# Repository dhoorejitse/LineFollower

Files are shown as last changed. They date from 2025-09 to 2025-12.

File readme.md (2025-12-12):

# LineFollower

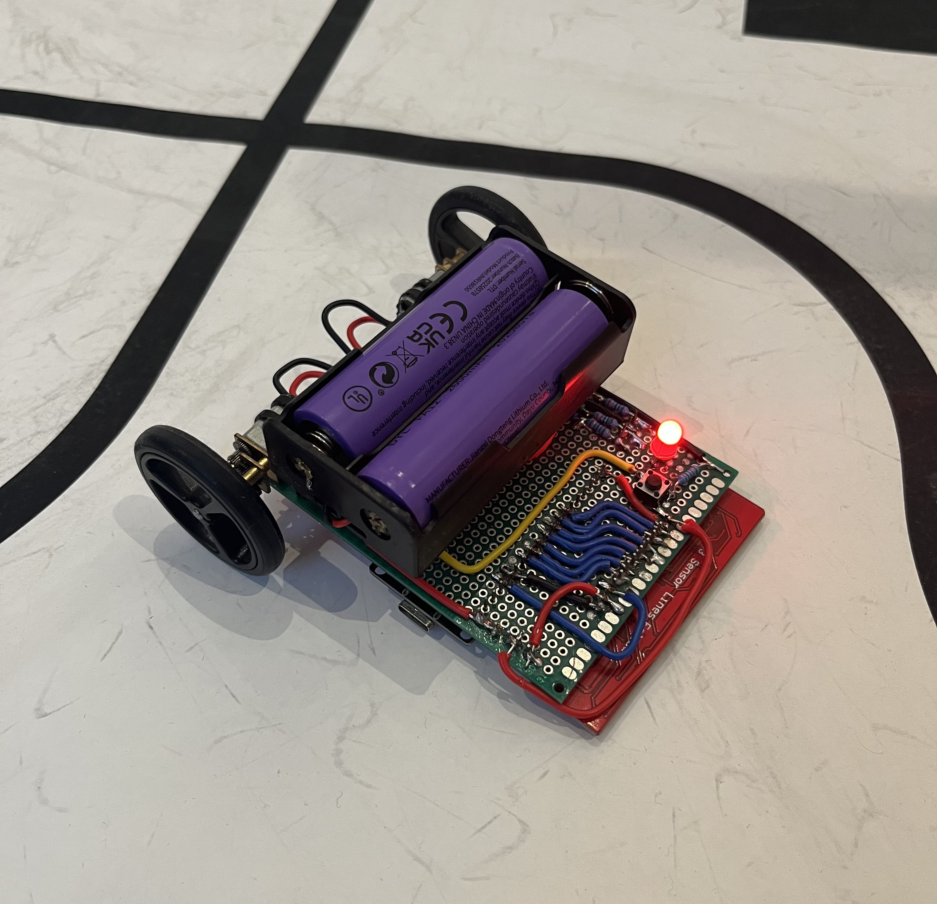
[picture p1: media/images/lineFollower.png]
lineFollower


## specifications

microcontroller: ESP32 NodeMCU Dev Board

motors: Aslong JGA12-N20-30 6V

h-bridge: DRV8833 H-Bridge Module

sensors: HY-S301

batteries: 2x18650

wireless communication: CP2102 (μC)

distance sensor - motors: 9cm

weight: 185g

speed: 0.6m/s

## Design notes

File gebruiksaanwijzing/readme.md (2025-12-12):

# Gebruiksaanwijzing

### gebruiken van esp32 in arduino IDE
* esp library intalleren
* boards toevoegen in preferences
* CP2102 drivers installeren

### opladen / vervangen batterijen
Het opladen van de batterijen gebreurd met een speciale batterijoplader die gemaakt is op de 18650 batterijen veillig en correct op te laden. Vervang de batterijen door de lege batterijen uit de houder te halen en vervang deze met opgeladen batterijen

### draadloze communicatie
#### verbinding maken
zorg dat de robot aanstaat (rgb led is rood/groen). Verbind vervolgens uw pc met bluetooth device "ESP32_BT_DJ". Maak vervolgens een seriele verbinding in PuTTy:
* Serial line: Gebruik de 2de bluetooth COM poort in de device manager
* Speed: 115200
* Connection type: Serial

#### commando's
help
debug  
run true
run false
set cycle [µs]  
set power [0..255]  
set diff [0..1]  
set kp [0..]  
set ki [0..]  
set kd [0..]  
calibrate black  
calibrate white  

### kalibratie
plaats de robot op een volledig zwarte ondergrond
* commando: calibrate black

plaats de robot op een volledig witte ondergrond
* commando: calibrate white

controlleer of de waarden binnen het gewenste waarden geven
* commando: debug

### settings
De robot rijdt stabiel met volgende parameters:  
* cycle: 1000
* power: 200
* diff: 0.4
* kp: 18
* ki: 0
* kd: 0.2

### start/stop button
de robot kan gestart worden op twee manieren:
* fysieke button vooraan de robot gelegen
* commando: run true/false

de status van de robot wordt aangeduid met behulp van een rgb led
* rode led: run false
* groene led: run true

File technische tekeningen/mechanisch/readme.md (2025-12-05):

# Technische tekeningen mechanisch

volgende zaken zitten in de mechanische technische tekeningen

* onderdelen
* samenstellingen

Deze werden vooral gebruikt in eerste instantie om na te gaan wat de beste positie was voor elk component + uitlijnen van wielen en sensor, etc.

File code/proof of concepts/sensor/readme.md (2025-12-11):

# Sensor - PoC
Deze PoC vererifieert de werking van volgende zaken:
- minimaal 6 sensoren kunnen onafhankelijk van elkaar worden uitgelezen (geen calibratie, normalisatie of interpolatie)
- Hierbij moet een zo groot mogelijk bereik van de AD converter benut worden (indien van toepassing)

Bij een correcte werking zal de sensor een hoge waarde geven bij lichte kleuren (max 4095) en een lage waarde bij donkere kleuren

https://github.com/user-attachments/assets/09217cbb-010d-4b2e-adb0-6ba14c347263

## Schema
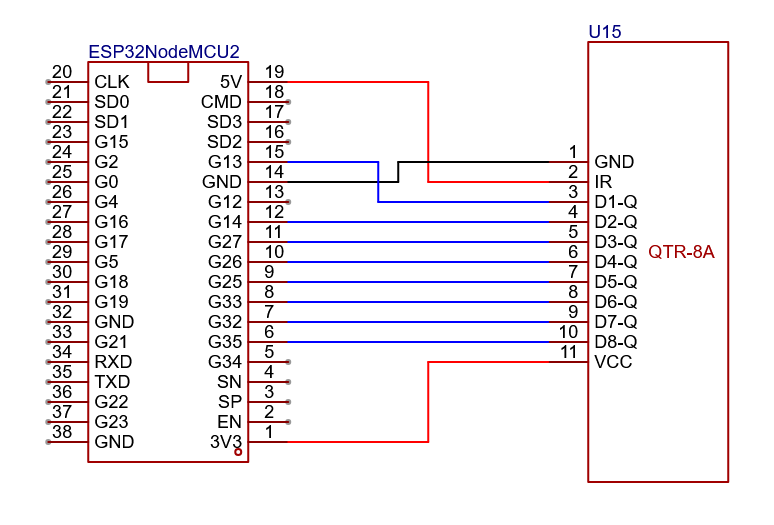
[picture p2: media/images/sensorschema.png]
Schema


## Stappenplan
- Sluit de componenten correct aan volgens bovenstaande schema
- Verbind de microcontroller met de pc
- Verify/Upload de code naar de mictrocontroller
- Verifieer de werking door te vergelijken met bovenstaande video

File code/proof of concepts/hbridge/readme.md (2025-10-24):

# H-Bridge - PoC
Deze PoC vererifieert de werking van volgende zaken:
- 2 motoren kunnen onafhankelijk van elkaar kunnen draaien
- motoren zijn (traploos) regelbaar in snelheid en draairichting

Bij een correcte werking zal eerst motor 1 traploos versnellen van stilstand tot zijn maximum snelheid, en vervolgens terug vertragen in de andere richting tot stilstand. Motor 2 herhaald deze werking.

https://github.com/user-attachments/assets/9430dffd-f219-440d-9be8-ca7bf7144678

## Schema
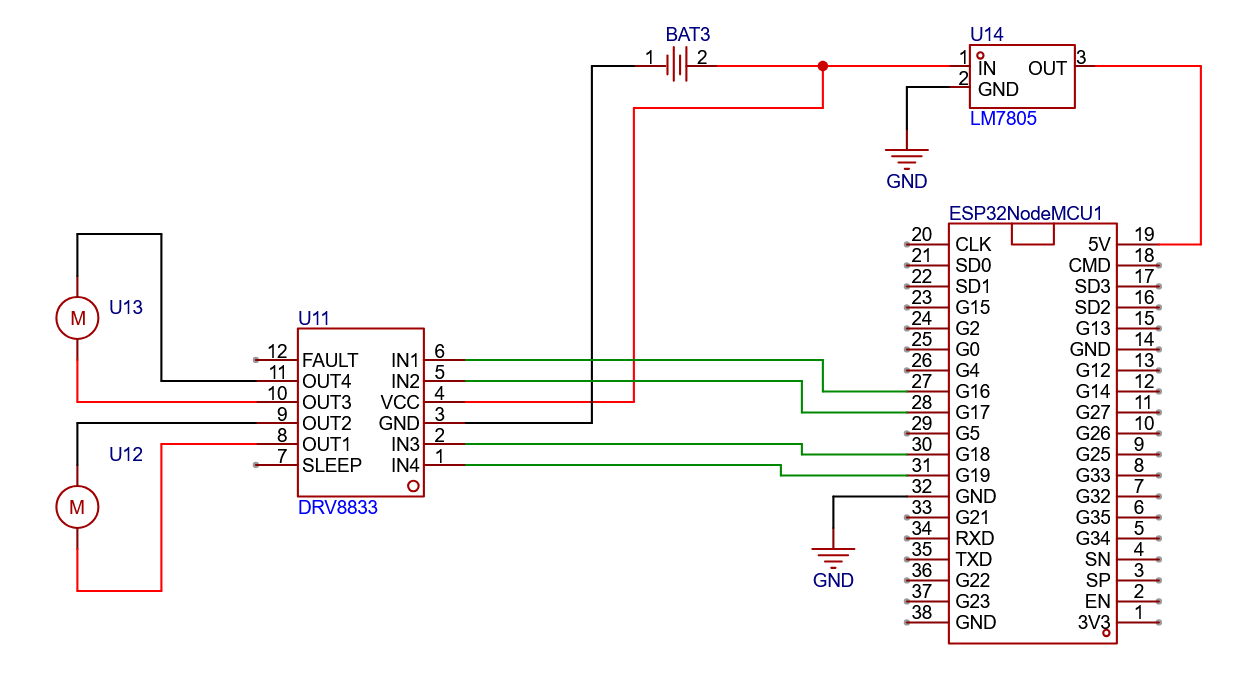
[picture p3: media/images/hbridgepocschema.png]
Schema


## Stappenplan
- Sluit de componenten correct aan volgens bovenstaande schema
- Verbind de microcontroller met de pc
- Verify/Upload de code naar de mictrocontroller
- Verifieer de werking door te vergelijken met bovenstaande video

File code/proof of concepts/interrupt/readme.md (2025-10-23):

# Interrupt - PoC
Deze PoC vererifieert de werking van volgende zaken:
- start/stop met drukknop
- gebruikmakend van een hardware interrupt

Bij een correcte werking zal de blink cyclus blijven doorlopen, wanneer de drukknop kortstondig word ingedrukt word de cyclus onderbroken en blijft de RGB led op wit. Bij een 2de keer drukken op de drukknop zal de cyclus hervatten

https://github.com/user-attachments/assets/07a7d600-da04-43f0-961d-6ccd3eb3b6cc

## Schema
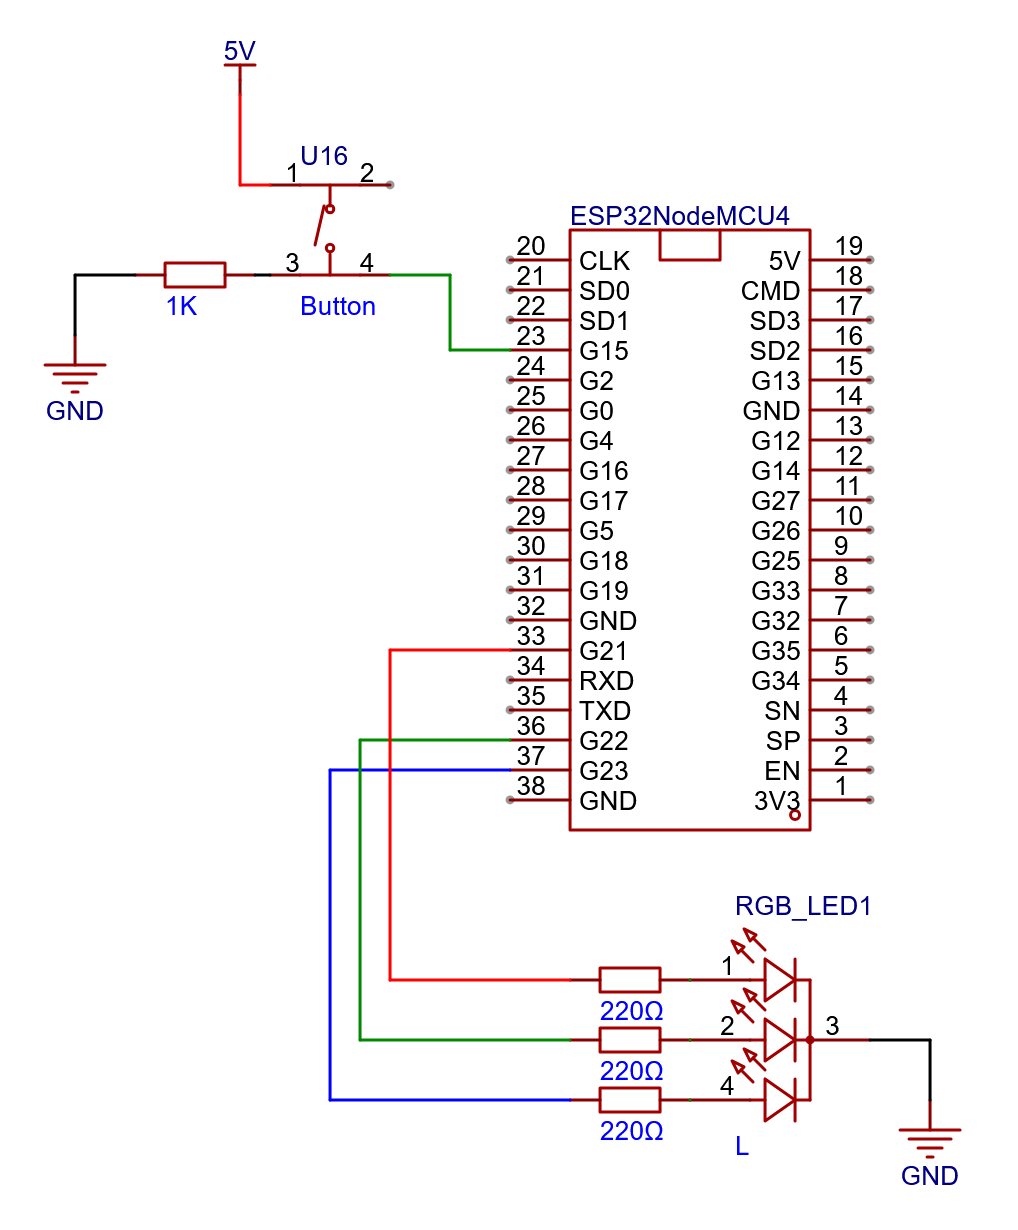
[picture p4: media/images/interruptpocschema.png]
Schema


## Stappenplan
- Sluit de componenten correct aan volgens bovenstaande schema
- Verbind de microcontroller met de pc
- Verify/Upload de code naar de mictrocontroller
- Verifieer de werking door te vergelijken met bovenstaande video

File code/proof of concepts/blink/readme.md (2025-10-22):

# Blink - PoC
Deze PoC vererifieert de werking van volgende zaken:
- compilen en uploaden van een programma naar de microcontroller lukt
- de klok frequentie van de microcontroller klopt

Bij een correcte werking knippert de RGB-led achtereenvolgens rood, groen en blauw, telkens 1 seconde aan en 1 seconde uit, waarna de cyclus zich herhaalt. Bij een opstart of reset van de microcontroller knippert de led 3 keer kortstondig wit.

https://github.com/user-attachments/assets/0f00047d-495a-4bb4-b6ac-76eb2669470c

## Schema
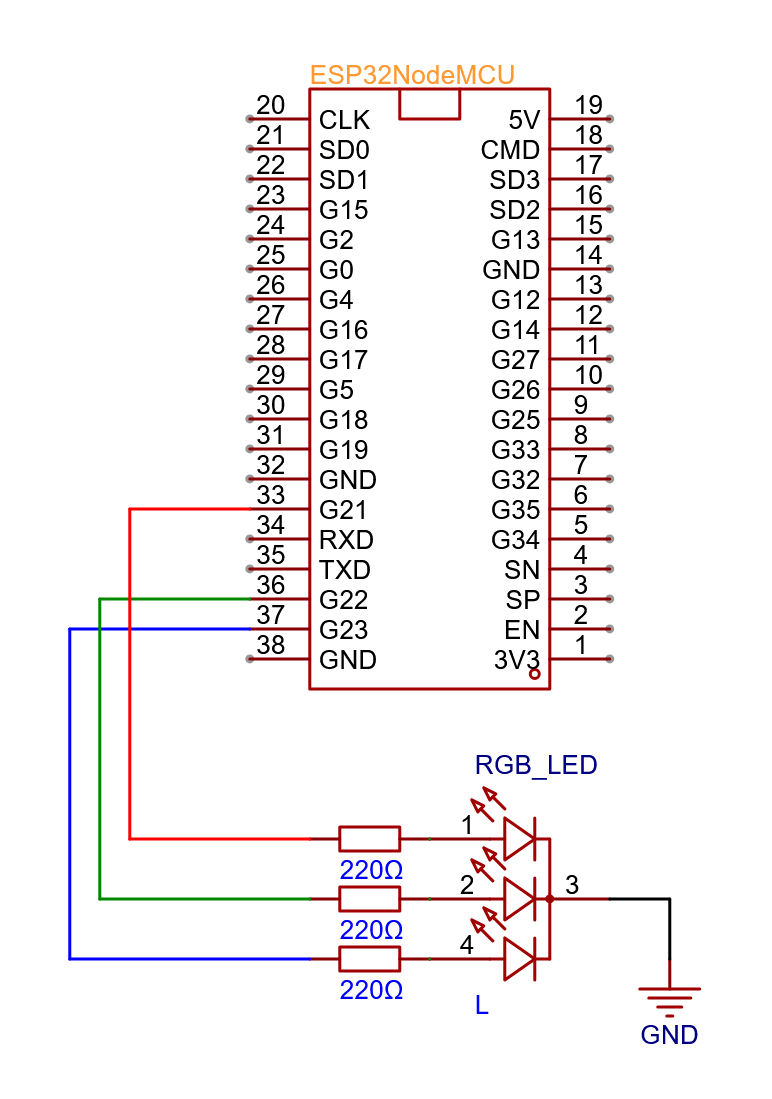
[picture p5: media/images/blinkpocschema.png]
Schema


## Stappenplan
- Sluit RGB led samen met weerstanden correct aan op de microcontroller volgens bovenstaande schema
- Verbind de microcontroller met de pc
- Verify/Upload de code naar de mictrocontroller
- Verifieer de werking door te vergelijken met bovenstaande video

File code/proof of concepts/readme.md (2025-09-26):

# Proof of Concepts

Een proof of concept is een combinatie van minimale hard- en software om eenvoudig aan te tonen dat iets werkt.  
Proof of concepts kunnen enerzijds als eerste poging dienen om een bepaald onderdeel van het project werkend te krijgen. Anderzijds kunnen ze tijdens het debuggen van het finale project dienen als test om eventuele hardware problemen te elimineren bij onduidelijke problemen.
<br />  
<br />
Een proof of concept bestaat uit
* een elektronisch schema (indien van toepassing)
* minimale code om de voorop gestelde zaken te demonstreren
* minimale uitleg / aandachtspunten
<br />
De elektronische schakelingen van de proof of concepts komen bij voorkeur overeen met deze van de uiteindelijke linefollower, zodat de code zonder aanpassingen op het finale project kan draaien.

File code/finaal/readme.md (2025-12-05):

# finaal programma

Dit is de volledige werkende code.

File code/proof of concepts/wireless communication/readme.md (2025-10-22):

# communicatie - PoC
Deze PoC vererifieert de werking van volgende zaken:
- er kan duplex gecommuniceerd worden tussen de microcontroller en een laptop
- gebruikmaken van PuTTy

Bij een correcte werking zal de seriële monitor berichten ontvangen van PuTTY, en zal PuTTy berichten ontvangen van de seriële monitor.

https://github.com/user-attachments/assets/d7bfd74a-13d0-45ac-b519-173b7eff39de

## Schema
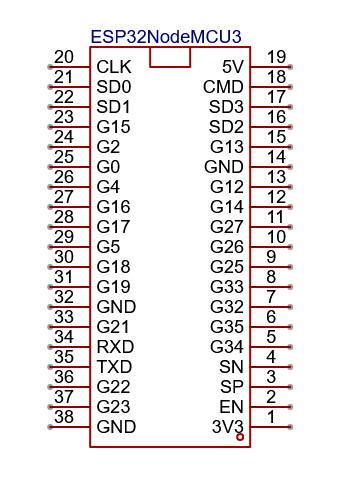
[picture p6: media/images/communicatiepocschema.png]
Schema


## Stappenplan
- Verbind de microcontroller met de pc
- Verify/Upload de code naar de mictrocontroller
- Controleer of de bibliotheek BluetoothSerial.h is geïnstalleerd
- Verbind met "ESP_BT_DJ" via bluetooth op laptop
- kijk in device manager welke COM word gebruikt door de bluetooth verbinding
- Connecteer via PuTTY met deze seriële COM en stel de correcte baudrate in
- Verifieer de werking door te vergelijken met bovenstaande video

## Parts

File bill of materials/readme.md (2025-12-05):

## bill of materials
<br />

|volgnummer|naam|omschrijving|nieuw/recup|kostprijs/stuk|aantal|subtotaal|
|----|---|---|---|---|---|---|
| 01 | ESP32 NodeMCU Dev Board | Development Board WiFi + Wireless CP2102 Dual Core 2.4GHz Microcontroller | Nieuw | € 8.50 | 1 | € 8.50 |
| 02 | Aslong JGA12-N20-30 | DC-Transmissiemotor 6V - 30:1 - 500RPM | Nieuw | € 4.50 | 2 | € 9.00 |
| 03 | DRV8833 H-Bridge Module | Motor Driver Module 1.5A Dual H-Bridge | Nieuw | € 1.50 | 1 | € 1.50 |
| 04 | HY-S301 | 8x IR Sensor (QTR-8A) | Nieuw | € 3.50 | 1 | € 3.50 |
| 05 | 18650 | Li-on Batterij - 2600mAh | Nieuw | € 2.50 | 2 | € 5.00 |
| 06 | Batterij Houder | 2 Slot 18650 Houder | Nieuw | € 1.50 | 1 | € 1.50 |
| 07 | Prototype Board | Dual Sided 90x70mm Board | Nieuw | € 0.50 | 1 | € 0.50 |
| 08 | Pololu Wiel 40x7mm | Siliconen Wielen - 3mm D-uitgaande as | Nieuw | € 2.50 | 2 | € 5.00 |
| 10 | LEGO blokje | Kleine lego blokjes gebruikt als steun vooraan | Recup | | 2 | |
| 11 | LED | | Recup | | 1 | |
| 12 | Knop | | Recup | | 1 | |
| 13 | Draad | 22AWG | Recup | | x | |
| 14 | Krimpkousen | | Recup | | x | |
| 15 | Soldeerdraad | | Recup | | x | |
| 16 | Pin Headers | Male + Female | Recup | | x | |
| 17 | Soldeerpasta | | Recup | | x | |
| | | | | | | € 34.5 |

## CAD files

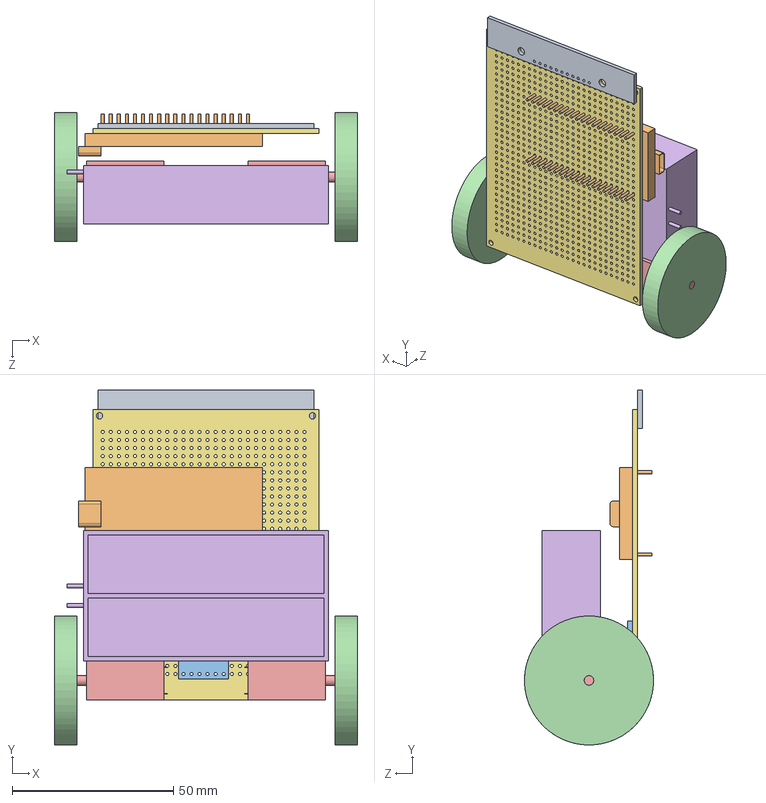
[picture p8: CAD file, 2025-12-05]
technische tekeningen/mechanisch/samenstellingen/LineFollower.SLDASM
94.0 x 110.0 x 40.0 mm
PrototypeBoard
BatteryHolder
Motor x 2
Wheel x 2
MotorDriver
Microcontroller
Sensor

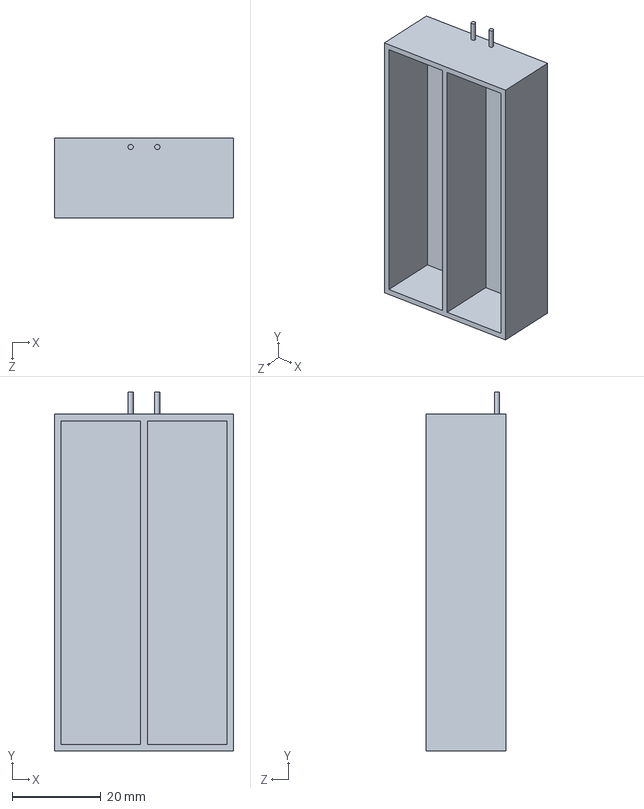
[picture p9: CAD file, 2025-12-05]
technische tekeningen/mechanisch/onderdelen/BatteryHolder.SLDPRT
40.5 x 81.0 x 18.0 mm

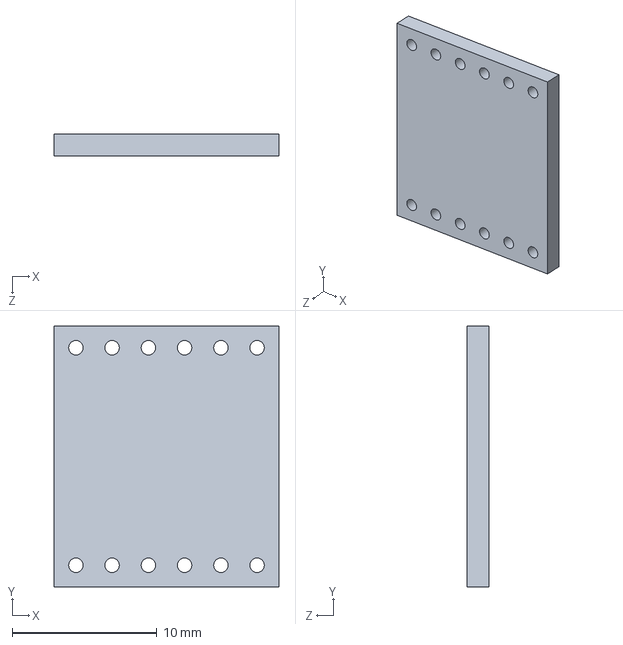
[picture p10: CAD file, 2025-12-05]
technische tekeningen/mechanisch/onderdelen/MotorDriver.SLDPRT
15.5 x 18.0 x 1.50 mm

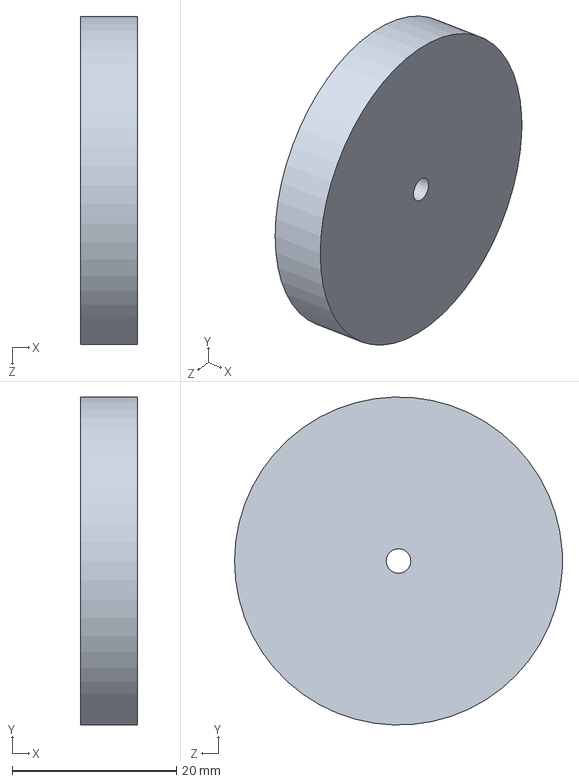
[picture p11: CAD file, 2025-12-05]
technische tekeningen/mechanisch/onderdelen/Wheel.SLDPRT
7.00 x 40.0 x 40.0 mm

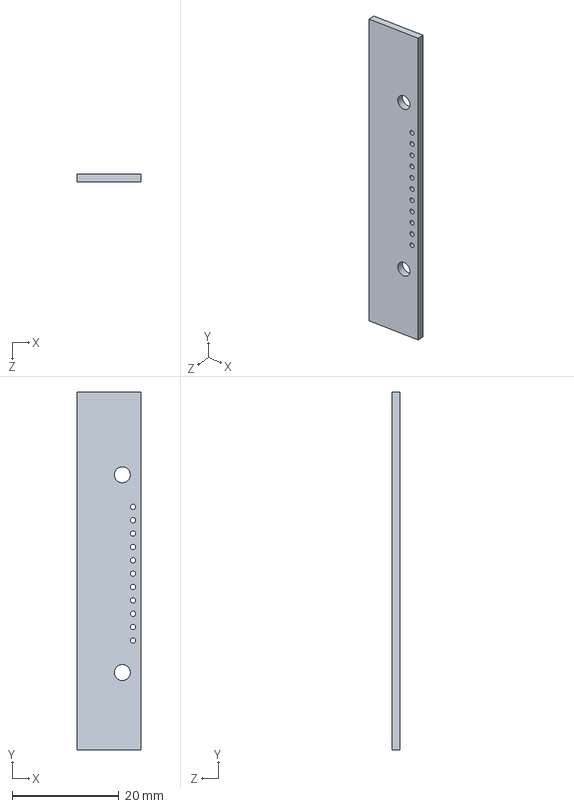
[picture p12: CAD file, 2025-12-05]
technische tekeningen/mechanisch/onderdelen/Sensor.SLDPRT
12.0 x 67.0 x 1.50 mm

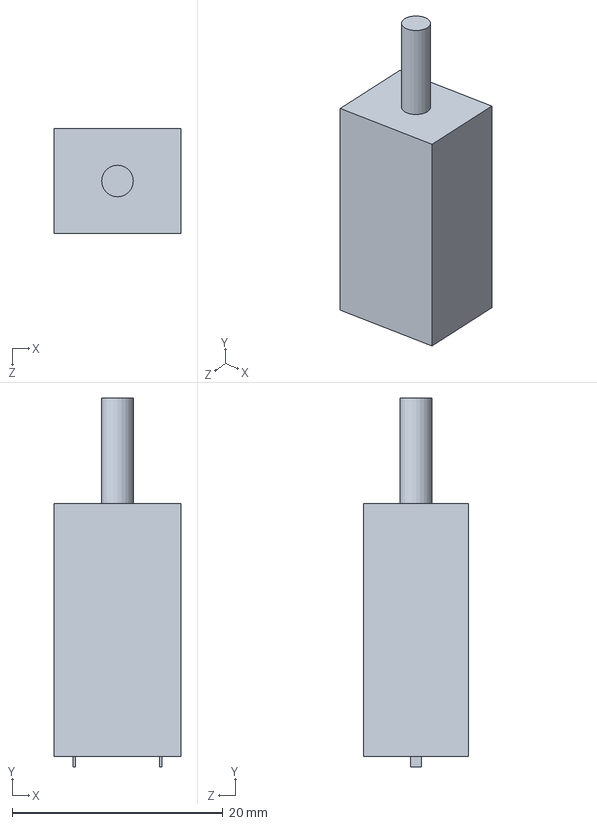
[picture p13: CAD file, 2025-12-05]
technische tekeningen/mechanisch/onderdelen/Motor.SLDPRT
12.0 x 35.0 x 10.0 mm

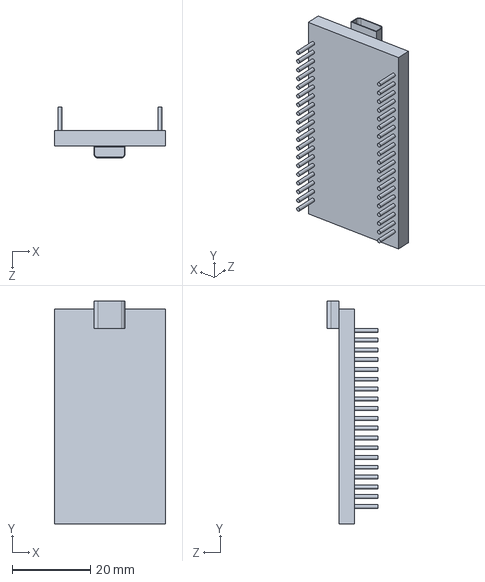
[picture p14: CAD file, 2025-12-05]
technische tekeningen/mechanisch/onderdelen/Microcontroller.SLDPRT
28.5 x 57.0 x 13.0 mm

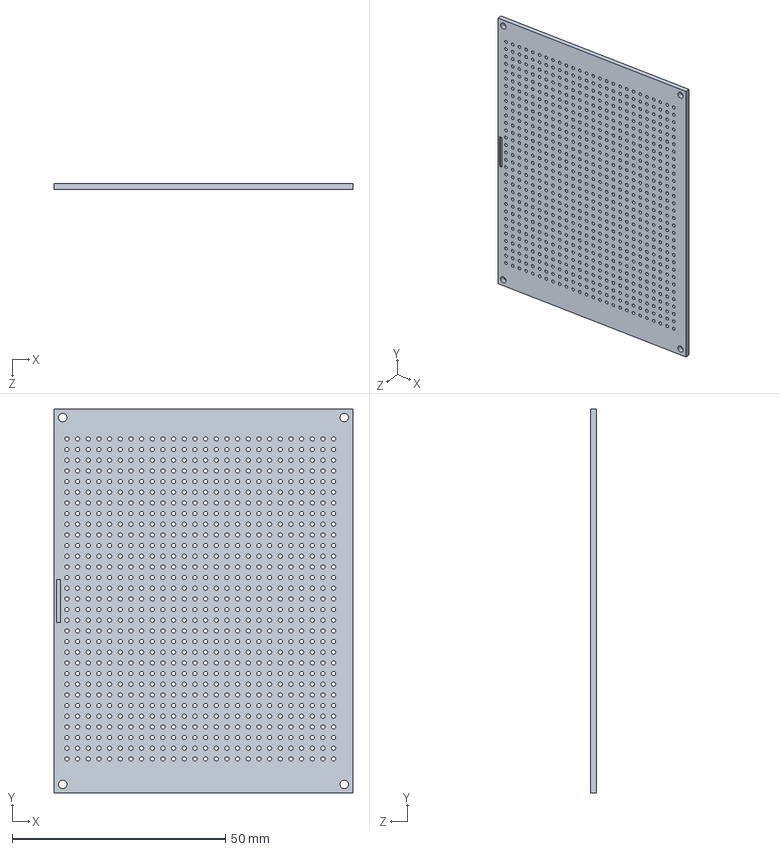
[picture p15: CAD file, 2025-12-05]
technische tekeningen/mechanisch/onderdelen/PrototypeBoard.SLDPRT
70.0 x 90.0 x 1.50 mm

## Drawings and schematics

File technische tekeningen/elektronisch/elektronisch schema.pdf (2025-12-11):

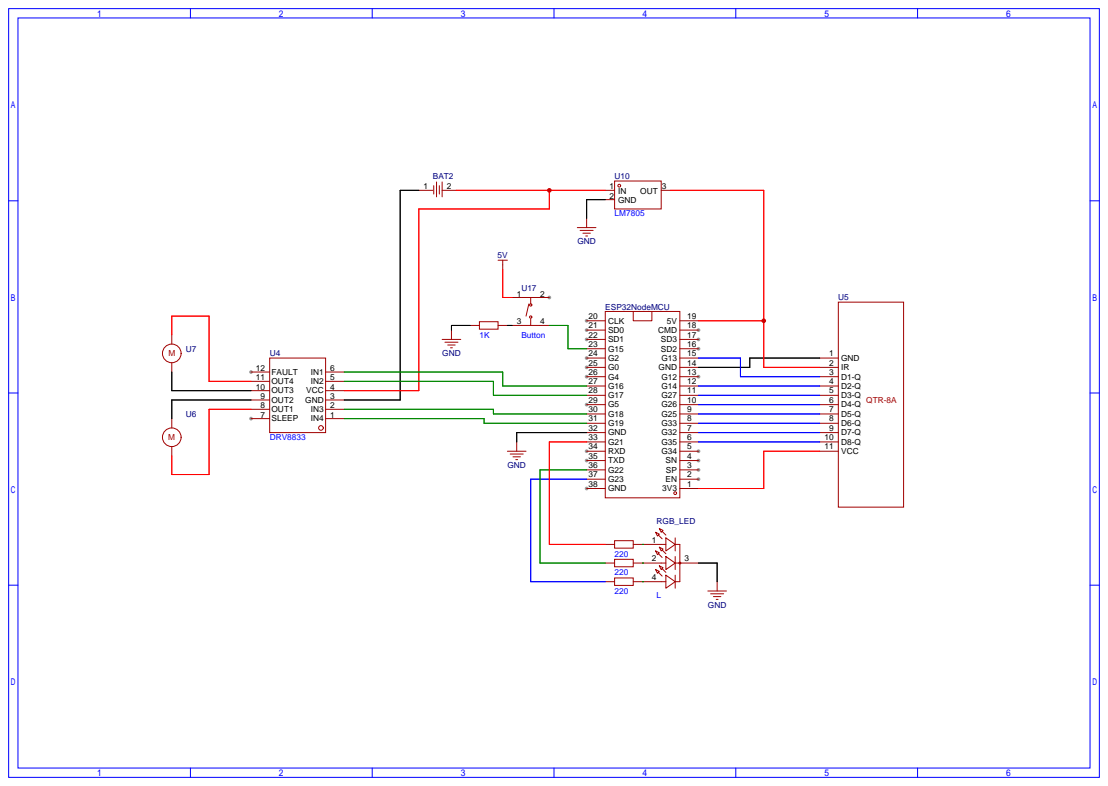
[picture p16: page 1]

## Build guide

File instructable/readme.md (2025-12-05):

# Instructable

### stap 1
bestel alle componenten uit de bill of materials  

### stap 2
soldeer de microcontroller, hbrug, sensor, en andere componenten op het prototype bord

### stap 3
soldeer de verbindingen tussen de componenten volgens de technische tekeningen

### stap 4 
maak boor 2 gaten op het einde van het prototype bord, bevesting met behulp van deze boringen de motoren aan het bord. (voeg secondelijm toe voor een sterkere verbinging)

### stap 5
schuur een blokje lego naar de juiste afmetingen en bevestig dit met secondelijm aan de sensor

### stap 6
soldeer pin headers op het bord en kleef pin headers vast aan de batterijhouder. Zo kan deze bevestigd worden aan het bord en snel los en vast gemaakt worden. Soldeer de verbindingen van de batterijhouder. (voeg krimpkousen toe om kortsluiting te voorkomen)

### stap 7
verbind de microcontroller met de pc gebruik maken van een USB-C kabel. Upload en compileer nu de finaal code naar de microcontroller, wacht tot deze volledig klaar is

### stap 8
de kabel mag nu uit de microcontroller worden getrokken

### stap 9
plaats de batterijen in de batterijhouder, de rgb led zou nu bij een correcte werking rood moeten branden

### stap 10
volg nu de stappen bij de gebruiksaanwijzing

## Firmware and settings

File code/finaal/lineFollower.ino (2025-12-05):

#include <Arduino.h>
#include "SerialCommand.h"
#include "EEPROMAnything.h"
#include <BluetoothSerial.h>

BluetoothSerial SerialPort;

void IRAM_ATTR handleButtonPress();
void updateRunLED();                  
void setColor(int r, int g, int b);

#define Baudrate 115200

#define MotorLeftForward 16
#define MotorLeftBackward 17
#define MotorRightForward 18
#define MotorRightBackward 19

const int pinR = 21;
const int pinG = 22;
const int pinB = 23;
const int buttonPin = 15;

volatile bool buttonPressed = false;
volatile unsigned long lastInterruptTime = 0;
const unsigned long debounceDelay = 200;

SerialCommand sCmd(SerialPort); // SerialPort for wired
bool debug = false;
bool run = false;
unsigned long previous, calculationTime; //set cycle time 2x calculationTime

const int sensor[] = {35,32,33,25,26,27,14,13};

struct param_t
{
  unsigned long cycleTime;
  int black[8]; //sensor
  int white[8]; //sensor
  int power;
  float diff;
  float kp;
  float ki;
  float kd;
  // add other paramaters here that need to be saved in memory 
} params;

int normalised[8];
float debugPosition;
float output;
float iTerm = 0;
float lastErr;

//*******************************************************************************// SETUP

void setup()
{
  Serial.begin(115200);
  SerialPort.begin("ESP32_BT_DJ");
  SerialPort.println("Verbonden");

  sCmd.setDefaultHandler(onUnknownCommand);
  sCmd.addCommand("help", onHelp);
  sCmd.addCommand("set", onSet);
  sCmd.addCommand("debug", onDebug);
  sCmd.addCommand("calibrate", onCalibrate);
  sCmd.addCommand("run", onRun);

  EEPROM.begin(512);
  EEPROM_readAnything(0, params);

  pinMode(pinR, OUTPUT);
  pinMode(pinG, OUTPUT);
  pinMode(pinB, OUTPUT);
  pinMode(buttonPin, INPUT);

  attachInterrupt(digitalPinToInterrupt(buttonPin), handleButtonPress, RISING);
  updateRunLED();

  SerialPort.println("ready");

  iTerm = 0;
}

//*******************************************************************************// LOOP

void loop()
{
  if (buttonPressed) 
  {
    buttonPressed = false;
    run = !run;
    if (run == false)
    {
      iTerm = 0;
    }
    updateRunLED();
  }

  sCmd.readSerial(); // listen and process serial commands

  unsigned long current = micros();
  if (current - previous > params.cycleTime)
  {
    previous = current;
    
    //measure & normalize
    for (int i = 0; i < 8; i++) normalised[i] = map(analogRead(sensor[i]), params.black[i], params.white[i], 0, 4096);

    //interpolate
    float position = 0;
    int index = 0;
    for (int i = 1; i < 8; i++) if (normalised[i] < normalised[index]) index = i;

    if (normalised[index] > 3000)
    {
      run = false; //can see if the robot is on a line or not, if not it, it will stop
      iTerm = 0;
      updateRunLED();
    }

    if (index == 0) position = -25;
    else if (index == 7) position = 25;
    else 
    {
      int sZero = normalised[index];
      int sMinusOne = normalised[index-1];
      int sPlusOne = normalised[index+1];

      float b = sPlusOne - sMinusOne;
      b = b / 2;

      float a = sPlusOne - b - sZero;

      position = -b / (2 * a);
      position += index;
      position -= 3.5;

      position *= 10;
    }
    debugPosition = position;

    float error = -position;
    output = 0;

    if (run) 
    {
      //proportional
      output = error * params.kp;

      //integration
      iTerm += params.ki * error;
      iTerm = constrain(iTerm, -510, 510);
      output += iTerm;

      //differentiation
      output += params.kd * (error - lastErr);
      lastErr = error;
    }
    else
    {
      iTerm = 0;
      output = 0;
    }

    output = constrain(output, -510, 510); //max en min PWM waarde motoren

    int powerLeft = 0;
    int powerRight = 0;

    if (run) if (output >= 0)
    {
      powerLeft = constrain(params.power + params.diff * output, -255, 255); //PWM motoren
      powerRight = constrain(powerLeft - output, -255, 255); //PWM motoren
      powerLeft = powerRight + output;
    }
    else
    {
      powerRight = constrain(params.power - params.diff * output, -255, 255); //PWM motoren
      powerLeft = constrain(powerRight + output, -255, 255); //PWM motoren
      powerRight = powerLeft - output;
    }

    // control motors
    analogWrite(MotorLeftForward, powerLeft > 0 ? powerLeft : 0);
    analogWrite(MotorLeftBackward, powerLeft < 0 ? -powerLeft : 0);
    analogWrite(MotorRightForward, powerRight > 0 ? powerRight : 0);
    analogWrite(MotorRightBackward, powerRight < 0 ? -powerRight : 0);
  }
  unsigned long difference = micros() - current;
  if (difference > calculationTime) calculationTime = difference;
}

//*******************************************************************************// SET

void onSet() //set commands
{
  char* param = sCmd.next();
  char* value = sCmd.next();

  if (strcmp(param, "cycle") == 0)
  {
    long newCycleTime = atol(value);
    float ratio = ((float) newCycleTime) / ((float) params.cycleTime);
    params.ki *= ratio;
    params.kd /= ratio;
    params.cycleTime = newCycleTime;
  } 
  else if (strcmp(param, "power") == 0) params.power = atol(value);
  else if (strcmp(param, "diff") == 0) params.diff = atof(value);
  else if (strcmp(param, "kp") == 0) params.kp = atof(value);
  else if (strcmp(param, "ki") == 0)
  {
    float cycleTimeInSec = ((float) params.cycleTime) / 1000000;
    params.ki = atof(value) * cycleTimeInSec;
  }
  else if (strcmp(param, "kd") == 0)
  {
    float cycleTimeInSec = ((float) params.cycleTime) / 1000000;
    params.kd = atof(value) / cycleTimeInSec;
  }
  else onUnknownParam((char*) param);

  EEPROM_writeAnything(0, params);
  EEPROM.commit();
}

//*******************************************************************************// CALIBRATE

void onCalibrate() //sensor calibration
{
  char* param = sCmd.next();

  if (strcmp(param, "black") == 0)
  {
    SerialPort.print("start calibrating black... ");
    for (int i = 0; i < 8; i++) params.black[i]=analogRead(sensor[i]);
    SerialPort.println("done");
  }
  else if (strcmp(param, "white") == 0)
  {
    SerialPort.print("start calibrating white... ");    
    for (int i = 0; i < 8; i++) params.white[i]=analogRead(sensor[i]);  
    SerialPort.println("done");      
  }
  else onUnknownParam((char*) param);

  EEPROM_writeAnything(0, params);
  EEPROM.commit();
}

//*******************************************************************************// DEBUG

void onDebug()
{
  SerialPort.print("cycle time: ");
  SerialPort.println(params.cycleTime);

  SerialPort.print("calculation time: ");
  SerialPort.println(calculationTime);
  calculationTime = 0;

  SerialPort.print("black: ");
  for (int i = 0; i < 8; i++)
  {
    SerialPort.print(params.black[i]);
    SerialPort.print(" ");
  }
  SerialPort.println(" ");

  SerialPort.print("white: ");
  for (int i = 0; i < 8; i++)
  {
    SerialPort.print(params.white[i]);
    SerialPort.print(" ");
  }
  SerialPort.println(" ");

  SerialPort.print("normalised: ");
  for (int i = 0; i < 8; i++)
  {
    SerialPort.print(normalised[i]);
    SerialPort.print(" ");
  }
  SerialPort.println(" ");

  SerialPort.print("position: ");
  SerialPort.println(debugPosition);

  SerialPort.print("power: ");
  SerialPort.println(params.power);

  SerialPort.print("diff: ");
  SerialPort.println(params.diff);

  SerialPort.print("kp: ");
  SerialPort.println(params.kp);

  float cycleTimeInSec = ((float) params.cycleTime) / 1000000;
  float ki = params.ki / cycleTimeInSec;
  SerialPort.print("ki: ");
  SerialPort.println(ki);

  float kd = params.kd * cycleTimeInSec;
  SerialPort.print("kd: ");
  SerialPort.println(kd);

  SerialPort.print("iTerm: ");
  SerialPort.println(iTerm);

  SerialPort.print("output: ");
  SerialPort.println(output);
}

//*******************************************************************************// INVALID COMMANDO

void onUnknownCommand(char* command)
{
  SerialPort.print("Unknown Command: \"");
  SerialPort.print(command);
  SerialPort.println("\"");
}

void onUnknownParam(char* param)
{
  SerialPort.print("Unknown Param: \"");
  SerialPort.print(param);
  SerialPort.println("\"");
}

void onUnknownValue(char* value)
{
  SerialPort.print("Unknown Value: \"");
  SerialPort.print(value);
  SerialPort.println("\"");
}

//*******************************************************************************// HELP

void onHelp()
{
  SerialPort.println("Available commands:");
  SerialPort.println("help");
  SerialPort.println("set cycle <value>");
  SerialPort.println("debug");
  SerialPort.println("calibrate <black/white>");
  SerialPort.println("run <true/false>");
  // add more if you register more commands
}

//*******************************************************************************// RUN

void onRun() //start or stop driving
{
  char* param = sCmd.next();

  if (strcmp(param, "true") == 0) 
  {
    run = true;
  } 
  else if (strcmp(param, "false") == 0)
  {
    run = false;
    iTerm = 0;
  }
  else 
  {
    onUnknownParam((char*) param);
    return;
  }
  updateRunLED();
}

void IRAM_ATTR handleButtonPress() {
  unsigned long t = millis();
  if (t - lastInterruptTime > debounceDelay) {
    buttonPressed = true;
    lastInterruptTime = t;
  }
}

void updateRunLED() {
  if (run) setColor(LOW, HIGH, LOW);   // green
  else     setColor(HIGH, LOW, LOW);   // red
}

//*******************************************************************************// RGB

void setColor(int r, int g, int b) {
  digitalWrite(pinR, r);
  digitalWrite(pinG, g);
  digitalWrite(pinB, b);
}

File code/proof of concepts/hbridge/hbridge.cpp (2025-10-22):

#include <Arduino.h>

// Motor pins
const int motorA_IN1 = 16;
const int motorA_IN2 = 17;
const int motorB_IN1 = 18;
const int motorB_IN2 = 19;

// PWM range
const int minSpeed = 0;
const int maxSpeed = 255;

// Delay tussen snelheidsveranderingen
const int delayTime = 200;

void setup() {
  Serial.begin(115200);
  delay(100);
  Serial.println("Setup klaar! Motoren test start...");

  pinMode(motorA_IN1, OUTPUT);
  pinMode(motorA_IN2, OUTPUT);
  pinMode(motorB_IN1, OUTPUT);
  pinMode(motorB_IN2, OUTPUT);
}

// Functie om motor te draaien
void driveMotor(int IN1, int IN2, int speed) {
  if (speed > 0) { // Vooruit
    analogWrite(IN1, speed);
    analogWrite(IN2, 0);
  } else if (speed < 0) { // Achteruit
    analogWrite(IN1, 0);
    analogWrite(IN2, -speed);
  } else { // Stop
    analogWrite(IN1, 0);
    analogWrite(IN2, 0);
  }
}

void loop() {
  // Motor A vooruit
  for (int s = 50; s <= maxSpeed; s += 5) {
    driveMotor(motorA_IN1, motorA_IN2, s);
    driveMotor(motorB_IN1, motorB_IN2, 0); // Motor B uit
    Serial.print("Motor A vooruit: ");
    Serial.println(s);
    delay(delayTime);
  }
  // Motor A achteruit
  for (int s = maxSpeed; s >= 50; s -= 5) {
    driveMotor(motorA_IN1, motorA_IN2, -s);
    driveMotor(motorB_IN1, motorB_IN2, 0);
    Serial.print("Motor A achteruit: ");
    Serial.println(s);
    delay(delayTime);
  }

  // Motor B vooruit
  for (int s = 50; s <= maxSpeed; s += 5) {
    driveMotor(motorA_IN1, motorA_IN2, 0);
    driveMotor(motorB_IN1, motorB_IN2, s);
    Serial.print("Motor B vooruit: ");
    Serial.println(s);
    delay(delayTime);
  }
  // Motor B achteruit
  for (int s = maxSpeed; s >= 50; s -= 5) {
    driveMotor(motorA_IN1, motorA_IN2, 0);
    driveMotor(motorB_IN1, motorB_IN2, -s);
    Serial.print("Motor B achteruit: ");
    Serial.println(s);
    delay(delayTime);
  }
}

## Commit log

2025-10-22 Update readme with ESP32 usage instructions
    Added instructions for using ESP32 in Arduino IDE.
2025-10-22 Add RGB LED control for ESP32
2025-10-22 Add H-Bridge motor control example
2025-10-24 Update component names in bill of materials
2025-10-24 Update item 04 in bill of materials
2025-12-05 Update bill of materials with LEGO block entry
2025-12-11 Fix distance sensor measurement unit casing
